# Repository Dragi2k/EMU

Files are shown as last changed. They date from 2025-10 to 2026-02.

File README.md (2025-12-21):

[][cc-by-nc-sa]

# EMU – Expandable Multi-material Unit
### A new take on a MMU by <a href="https://github.com/DW-Tas">DW-Tas</a> and <a href="https://github.com/igiannakas">igiannakas</a><br/>
<a href="https://ko-fi.com/O5O5OCC0K"> Ko-Fi</a>

**Introducing the EMU, the Expandable Multi-material Unit from down under.** The EMU is a modular, flexible, upgradable, reliable and service-friendly MMU designed around the proven filamentalist V3 platform.

The EMU supports any number of lanes and base configurations; whether it is a **single lane setup** to assist filament loading, a **dual lane configuration** for endless spool, or a **multi-lane, multi base unit setup** for multi-material printing. It is also **expandable**, with no re-printing of parts required when upgrading from a 2 lane to a multiple lane setup.

<p align="center">
  
</p>

### Table of Contents
- [Design Objectives & Key Features](#design-objectives)
- [Render Gallery](#render-gallery)
- [Prints Gallery](#prints-gallery)
- [Documentation](/docs)
  - [BOM, Printing, Assembly and Wiring instructions](/docs/assembly_wiring)
  - [Software Setup and Calibration](/docs/software_setup)
  - [Slicer setup and optimisation for multi color prints](/docs/software_setup/05-slicer-setup.md)
- [License](#this-work-is-licensed-under-a)

### Highlights
- **Modular & Expandable** design, able to add lanes anytime and in any configuration. No reprints when upgrading from a 2 lane setup.
- **One screw or tool-free** access and servicing, even mid-print.
- **Sealed dry boxes** able to maintain humidity in the 15% range (with silica gel) or 5–8% range (with molecular sieves) for weeks.  
- **Humidity sensors** per lane for filament environmental monitoring.
- **Reliable endless spool** with no chance of the rewound filament interfering with neighbouring rolls.
- **Off-the-shelf electronics** (EBB42 with EBB36 also fully compatible).  
- **Per-lane controls** - eject button + LEDs.

<p align="center">
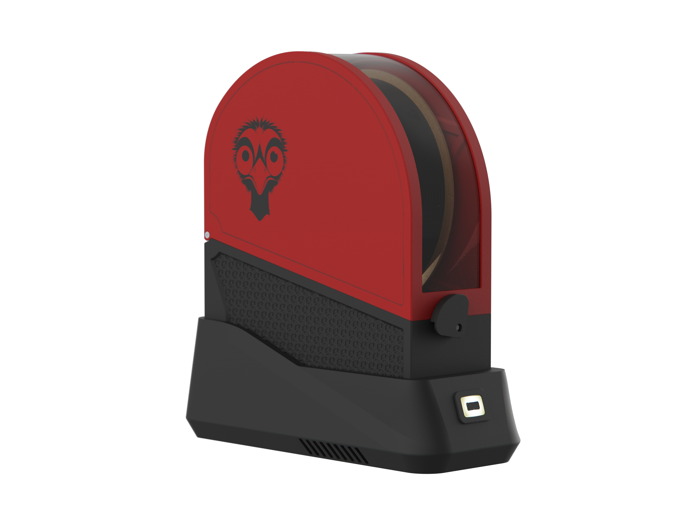
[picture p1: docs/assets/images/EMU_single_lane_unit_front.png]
  
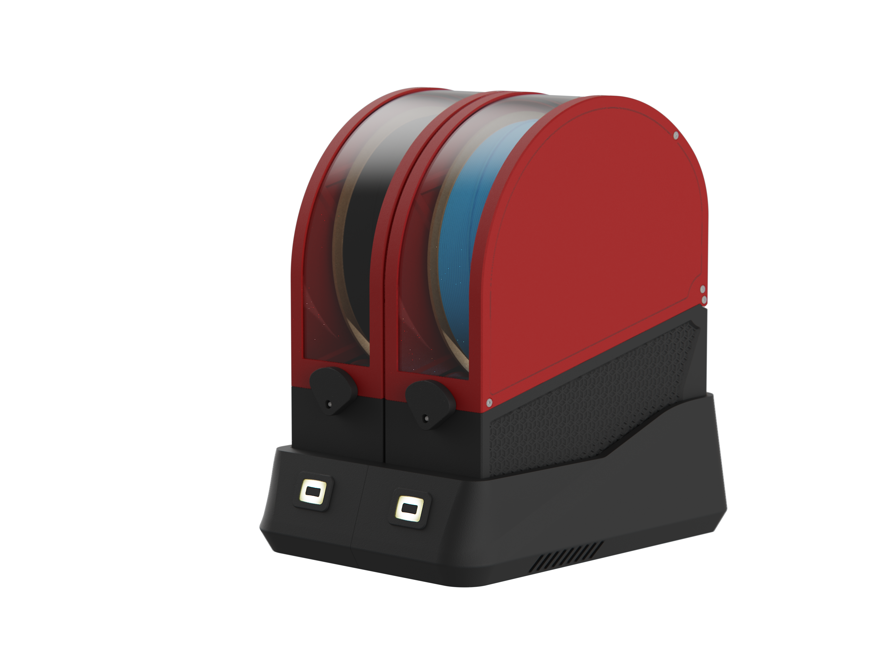
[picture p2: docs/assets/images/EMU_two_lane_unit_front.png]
  
</p>

## Design Objectives

### Modularity & Upgradeability  
Each lane is fully self-contained, so you can choose **exactly how many lanes you need and group them as you like**. You can also **mix and match** lanes across multiple base units, or use a stand-alone single lane for extruder loading and print assistance. 

Expanding later is also straightforward. Just print lane expanders for the base and add another dry box assembly. There is no need to reprint or replace existing parts when upgrading from a 2 lane base. 

### Ease of Servicing 
All electrical and mechanical components are either **one screw or completely tool-free and immediately accessible**, making live troubleshooting possible even during a print. 

Access to the electronics is easy - just lift the dry box off its base for full access. The stepper tensioning screw is accessible without any dissassembly allowing on the fly tuning of filament grip. Finally, removing the filamentalist, stepper and stepper assembly is possible via one screw.

### Sealed Dry Boxes  
Each spool sits in its own purpose built, **fully sealed dry box with an integrated desiccant holder**. The boxes use foam cord in areas of potential air ingress to create a tight seal, with the clear 1.5mm PETG/PC panel also offering visibility inside the dry box.

The dry boxes can maintain humidity in the 15% range (with silica gel) or 5–8% range (with molecular sieves) for weeks. Finally, as each dry box is self contained, opening one to reload filament, doesn’t disturb its neighbours, extending the effective desiccant life.

<p align="center">
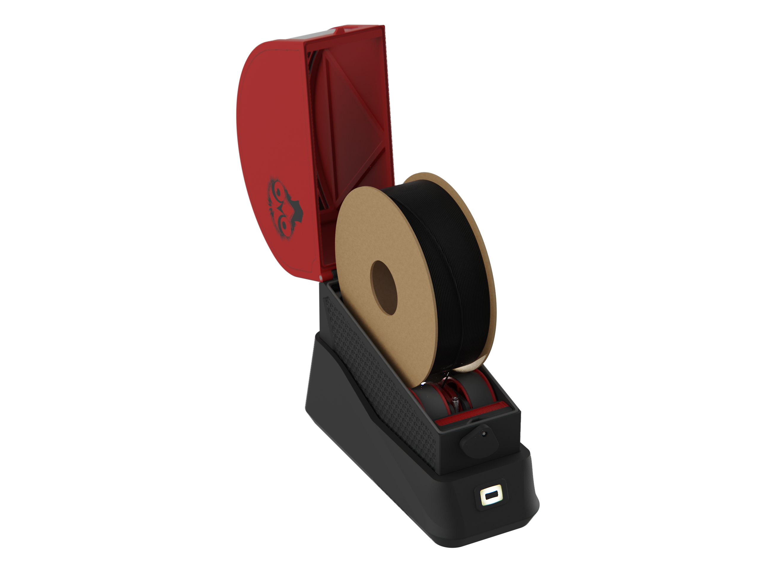
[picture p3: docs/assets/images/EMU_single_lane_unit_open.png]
  
</p>

### Integrated Humidity Sensors 
Each lane monitors its own environment, letting you know when it’s **time to refresh the desiccant**. The humidity sensors are integrated into Mainsail (and optionally in Home Assistant for historical data tracking via the mainsail HA integration).

### Endless Spool Reliability
Dual pre-stepper sensors ensure **consistent run-out detection** and reliable re-wind, as the filament is always gripped by the stepper hobbed gear assembly. 

In addition, the isolated boxes ensure that any left over, rewound, filament cannot interfere with neighbouring lanes, **preventing a jam**.

### Built on the Filamentalist
The lane assembly is based on the proven **[filamentalist V3 design with 688 bearings](https://github.com/Enraged-Rabbit-Community/ERCF_v2/tree/master/Recommended_Options/Filamentalist_Rewinder/Filamentalist_FV3_Rewinder)**, with no modifications necessary. 
- Existing 688 bearing version filamentalist parts can be reused when building an EMU.
- Optionally, the revised tensioner mount further improves pre-stepper switch actuation.
- Wide spool size compatibility - built on the 74mm filamentalist stock setup and fits even KVP filament spools.

<p align="center">
  
  
</p>

### Integrated Filament Driving Stepper 
Each lane has its own driving stepper inside the dry box, resulting in a compact, **fully self-contained mechanical design**. In case of mechanical issue, you can swap out filamentalist assemblies with 3 screws, unplugging 2 JST plugs and unplugging the bowden tube. 

In addition, you can **swap out complete dry boxes** by unplugging two JST plugs and the bowden tube. This is helpful if you want to maintain a particularly moisture sensitive filament undisturbed when swapping it out from the EMU.

### Simple Electronics
The recommended BOM uses **readily available EBB42 boards** (with EBB36 fully compatible). MMB v2 boards can also be reused, though without humidity sensing due to I²C limitations and a slightly more intricate wiring.

In addition, **each lane has its own ventilation fan**, ensuring the stepper drivers do not overheat, even when the unit is placed on top of a hot printer. With the EBB42 and EBB36, the ventilation fans can also be speed controlled to minimize noise.

### Easy mounting
The EMU base assembly can be securely **mounted on extrusions** or using **rubber feet** directly on the printer or besides it. In either case the **electronics remain accessible** without needing to remove the unit from its mounts.

### Per-lane Controls  
Each lane includes its own eject button, status LED, and a filament colour LED that illuminates the dry box. 

## Render Gallery
<p align="center">
  
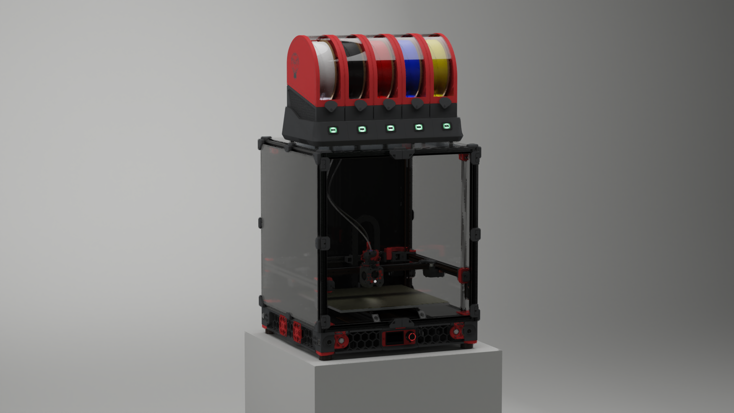
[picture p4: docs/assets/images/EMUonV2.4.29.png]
  
</p>
<p align="center">
  
  
</p>
<br/>

## Prints Gallery
<p align="center">
  1 (4)
  1 (5)
  1 (2)
  1 (3)
</p>

## This work is licensed under a
[Creative Commons Attribution-NonCommercial-ShareAlike 4.0 International License][cc-by-nc-sa].

[][cc-by-nc-sa]

[cc-by-nc-sa]: http://creativecommons.org/licenses/by-nc-sa/4.0/
[cc-by-nc-sa-image]: https://licensebuttons.net/l/by-nc-sa/4.0/88x31.png
[cc-by-nc-sa-shield]: https://img.shields.io/badge/License-CC%20BY--NC--SA%204.0-lightgrey.svg

## License clarification regarding non-commercial use:
The non-commercial aspect of this license is for cases where EMU is the product, not the use of EMU to create products.<br/>
I.e. If you wish to sell EMU as a product, you would need to seek a commercial license before doing so. </br>
It is NOT intended to prevent the use of EMU with a printer that you use to provide commercial services. If you want to run EMU in your print farm, go right ahead.

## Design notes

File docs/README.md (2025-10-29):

[][cc-by-nc-sa]

# EMU – Expandable Multi-material Unit Documentation
### A new take on a MMU by <a href="https://github.com/DW-Tas">DW-Tas</a> and <a href="https://github.com/igiannakas">igiannakas</a><br/>
<a href="https://ko-fi.com/O5O5OCC0K"> Ko-Fi</a>

<p align="center">
  
</p>

## Step 1: [Printing, assembly and wiring](/docs/assembly_wiring)
This page explains the EMU assembly and wiring. It links the BOM, detailed print settings for all of the EMU parts, including tips on how to achieve the optimal print reseults. It also includes the assembly videos, covers multi-lane and single-lane wiring for both EBB42/36 boards.

- [BOM](/docs/assembly_wiring/#bom)
- [Print Settings](/docs/assembly_wiring/#print-settings)
  - [Filamentalist components and Lane stepper components](/docs/assembly_wiring/#filamentalist-components-and-lane-stepper-components)
  - [Dry Box components](/docs/assembly_wiring/#dry-box-components)
  - [Base unit components](/docs/assembly_wiring/#base-unit-components)
- [Assembly Videos](/docs/assembly_wiring/#assembly-videos)
  - [Part 1: Filamentalist and Stepper Assembly Guide](/docs/assembly_wiring/#part-1-filamentalist-and-stepper-assembly-guide)
  - [Part 2: Drybox Assembly Guide](/docs/assembly_wiring/#part-2-drybox-assembly-guide)
  - [Part 3: Base Assembly Guide](/docs/assembly_wiring/#part-3-base-assembly-guide)
  - [Part 4: Electronics Assembly Guide](/docs/assembly_wiring/#part-3-base-assembly-guide)
- [Wiring Instructions and Diagrams](/docs/assembly_wiring/#wiring-instructions-and-diagrams)

## Step 2: [EMU board setup](/docs/software_setup/01-board-setup.md)
This page explains in detail how to setup your EMU boards with CANBus, how to flash Katapult and klipper as well as the procedure to update the klipper firmware.

- [Setting up CAN Bus](/docs/software_setup/01-board-setup.md#setting-up-can-bus)
- [Flashing the EBB boards](/docs/software_setup/01-board-setup.md#flashing-the-ebb-boards)
- [Updating the boards with the latest klipper version](/docs/software_setup/01-board-setup.md#updating-the-boards-with-the-latest-klipper-version)

## Step 3: [Happy Hare setup](/docs/software_setup/02-happy-hare-setup.md)
This page explains the step by step process to install and set up Happy Hare, the MMU management software that drives the EMU.

- [Installing Happy Hare](/docs/software_setup/02-happy-hare-setup.md#installing-happy-hare)
- [Configuring the EMU hardware](/docs/software_setup/02-happy-hare-setup.md#configuring-the-emu-hardware)
- [Configuring Happy Hare parameters](/docs/software_setup/02-happy-hare-setup.md#configuring-happy-hare-parameters)
      
## Step 4: [Calibration and startup](/docs/software_setup/03-calibration-and-startup.md)
This page explains the step by step process to calibrate the unit and the initial start up checks required to ensure successful first operation.

- [Lane rotation distance calibration](/docs/software_setup/03-calibration-and-startup.md#lane-rotation-distance-calibration)
- [Bowden tube calibration](/docs/software_setup/03-calibration-and-startup.md#bowden-tube-calibration)
- [First start up](/docs/software_setup/03-calibration-and-startup.md#first-start-up)

## Step 5: [Slicer setup and optimisation for multi color prints](/docs/software_setup/05-slicer-setup.md)
Describes the mangatory Orca slicer setup required for single extruder multi-material printing, including print profile settings to achieve optimal quality results.

- [Orca slicer mandatory setup](/docs/software_setup/05-slicer-setup.md#orca-slicer-mandatory-setup)
- [Orca slicer profile tuning for multi-color printing](/docs/software_setup/05-slicer-setup.md#orca-slicer-profile-tuning-for-multi-color-printing)

## Next steps
Once you have completed the guide above you should have a fully functioning EMU unit! Optionally you can also set up:
1. Klipper screen integration: https://github.com/moggieuk/Happy-Hare/wiki/KlipperScreen
2. Mainsail / Fluid MMU panel: https://github.com/moggieuk/Happy-Hare/wiki/Mainsail-Fluidd-Integration
3. Spoolman: https://github.com/moggieuk/Happy-Hare/wiki/Spoolman-Support

In addition, to add further lanes, follow  the instructions here: [Expanding the unit](/docs/software_setup/04-expanding-the-unit.md)

## Seeking help

The Happy Hare discord is a great resource to help you going. Both in the general channel as well as the dedicated EMU channel. Link to the discord can be found here: https://discord.gg/aABQUjkZPk

#### This work is licensed under a
[Creative Commons Attribution-NonCommercial-ShareAlike 4.0 International License][cc-by-nc-sa].

[][cc-by-nc-sa]

[cc-by-nc-sa]: http://creativecommons.org/licenses/by-nc-sa/4.0/
[cc-by-nc-sa-image]: https://licensebuttons.net/l/by-nc-sa/4.0/88x31.png
[cc-by-nc-sa-shield]: https://img.shields.io/badge/License-CC%20BY--NC--SA%204.0-lightgrey.svg

### License clarification regarding non-commercial use:
The non-commercial aspect of this license is for cases where EMU is the product, not the use of EMU to create products.<br/>
I.e. If you wish to sell EMU as a product, you would need to seek a commercial license before doing so. </br>
It is NOT intended to prevent the use of EMU with a printer that you use to provide commercial services. If you want to run EMU in your print farm, go right ahead.

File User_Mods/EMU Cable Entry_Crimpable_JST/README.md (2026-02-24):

# EMU Cable Entry with Cimpable JST sockets

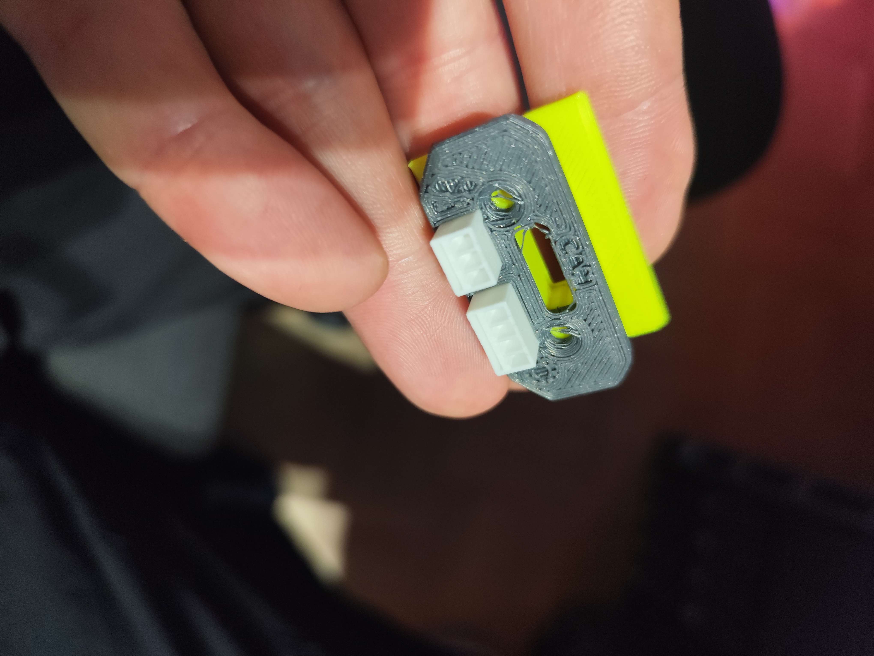
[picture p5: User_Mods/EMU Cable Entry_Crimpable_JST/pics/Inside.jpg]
Inside


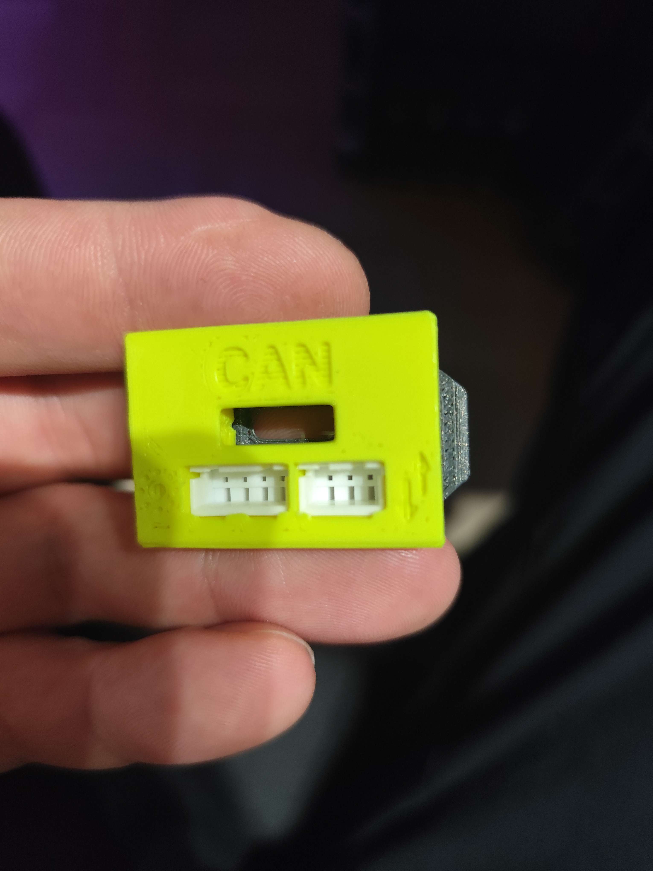
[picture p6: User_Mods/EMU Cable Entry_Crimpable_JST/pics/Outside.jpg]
Outside


for the 3 and 4 pin use these : 

https://de.aliexpress.com/item/1005008063018644.html

https://de.aliexpress.com/item/1005007287524489.html

or

https://de.aliexpress.com/item/1005009495585754.html

you need :

1x 3 pin
1x 4 pin 
per In/outled

the can bus is the origin from the BOM

by Dragi2k

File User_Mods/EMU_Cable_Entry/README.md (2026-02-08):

# EMU Cable Entry blank plate

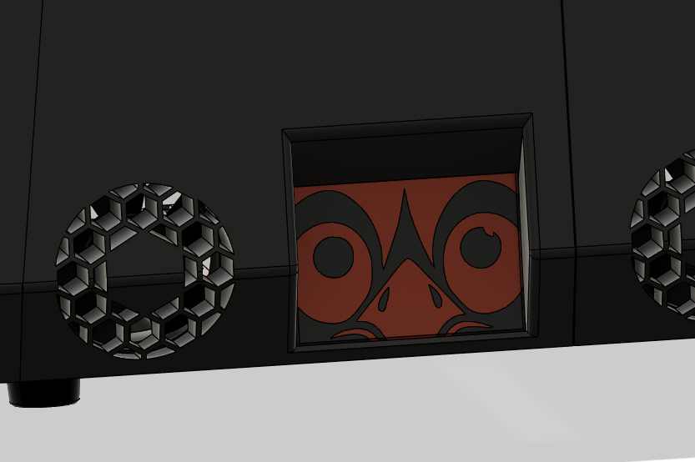
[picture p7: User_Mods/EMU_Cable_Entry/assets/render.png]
render of the plate


For those with multimaterial capabilities, or to swap in after building the EMU.  
A blank cable entry plate for the side where you don't have cables coming in. With some extra EMU flair

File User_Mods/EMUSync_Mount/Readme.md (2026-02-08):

# EMUSync_Mount

Wanted to stabalized the PSF body and not have it hanging loose in the bowden path.   Maing sure the bowden path did not have any sharp bends, curves and having the PSF as close to the EMU as possible drove the overall design.    The mounts allow for perpendicular (hanging off the back) and parallel to the extrusion mounting.

---

## Overview

It's specifically designed for the square body EMUSync in the EMU repo.   If another body type is used, a new clamp could be mounted directly to the mounting plate.   The entire clamp system can be printed without supports, and printed in the orientation with the largest flat side down.   The STL's and STEP's are filed in print orinentation.    

Assembly is straight forward simply print the parts, insert the adaptor plate in 1 of the peg holes, insert the secondary securing peg, insert the square nuts, use M3x14mm screws to secure the adaptor plate.  for best results use a M3x6 or M3x8 BHS for mounting the clamp to the adaptor plate.   M3x8mm screw to secure the clamp top

both 4040 and 2020 mounts are avialable and with the edges of the mount extended to act as panel clamp.

## Bill of Materials

### Fasteners
- 2 × M3x14 SHCS
- 2 x M3x8 SHCS
- 1 x M3 x 8 BHCS
- 3 x M3 Square Nut

### Hardware
- 1 Heat-set inserts M3×5×4)
- 3 M3 Square Nut







## Credits

This project was created by @woodworker.

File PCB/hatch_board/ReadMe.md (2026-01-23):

## EMU Wiring Hatch Board

The **EMU Wiring Hatch Board** is a dedicated PCB designed for EMU to make wiring and assembly easier and more convenient. It replaces the printed hatch ([Box_wiring_hatch](https://github.com/DW-Tas/EMU/blob/main/STL/Box/%5Ba%5D_Box_wiring_hatch.stl)), eliminates the need to solder the Filamentalist assembly wires to the JST connectors, and removes the need to use silicone to seal gaps around the JST connector.

The EMU Wiring Hatch Board was designed and developed by <a href="https://github.com/kashine6">kashine6</a>.

## Key Features

1. **Eliminates the need to solder wires directly to JST connectors**
   - Simplifies assembly
   - Reduces soldering complexity
   - Improves maintainability, as the Filamentalist assembly can be easily unplugged from inside the base unit

2. **Simplified pre-stepper sensor connections**
   - The two pre-stepper switches no longer need to be soldered in parallel. Instead, solder the sensor and ground wires to each switch individually, then plug them into the board separately.

3. **Easier box sealing**
   - Removes the need to use silicone to seal the JST connector on the hatch cover.

4. **Wire labeling**
   - Wire labels on the PCB silkscreen reduce the chance of wiring errors during assembly.

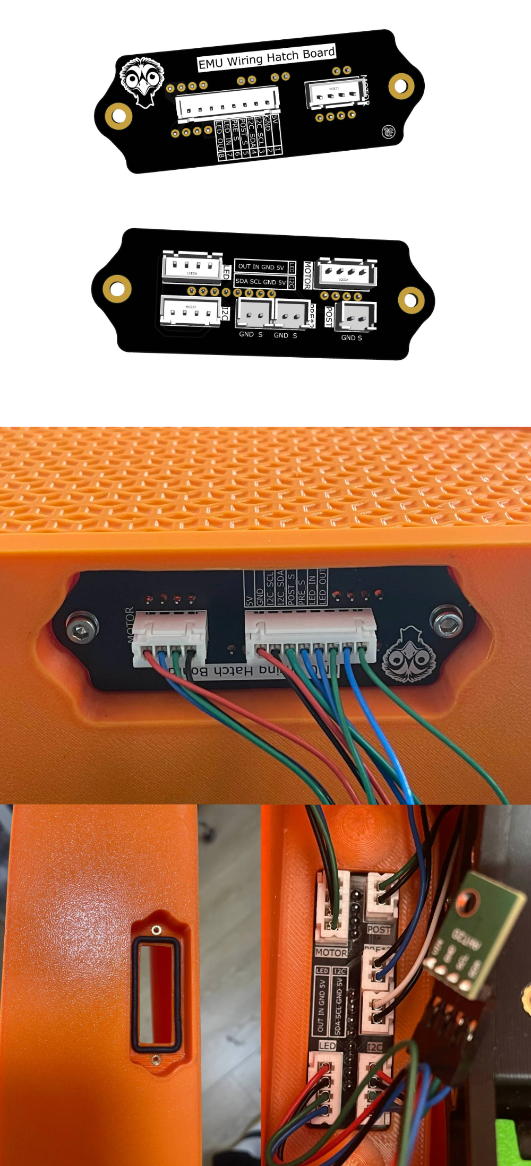
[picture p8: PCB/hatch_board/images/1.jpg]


## BOM variations vs. baseline EMU BOM
Due to the PCB being thinner than the printed box wiring hatch, **the 2x M3x8mm FHCS screws are now replaced by 2x M3x6 BHCS/SHCS screws**.

If buying pre-assembled, the corresponding straight through hole PCB header JST connectors in the BOM are no longer needed (1x JST XH 8 pin plug and 1x JST XH 4 pin plug).

If making your own and soldering the JST headers, you'll need the below JST PCB headers:
- 3x JST XH Series Straight Through Hole PCB Header, 4 Contact
- 3x JST XH Series Straight Through Hole PCB Header, 2 Contact
- 1x JST XH Series Straight Through Hole PCB Header, 8 Contact **(part of the EMU BOM)**
- 1x JST XH Series Straight Through Hole PCB Header, 4 Contact **(part of the EMU BOM)**

## Sourcing
The hatch board PCBs can be sourced from [kashine6 shop](https://www.aliexpress.com/item/1005011529532141.html) in packs of 5, or ordered DIY from JLCPCB or alternative PCB manufacturers.

## This work is licensed under a
[Creative Commons Attribution-NonCommercial-ShareAlike 4.0 International License][cc-by-nc-sa].

[][cc-by-nc-sa]

[cc-by-nc-sa]: http://creativecommons.org/licenses/by-nc-sa/4.0/
[cc-by-nc-sa-image]: https://licensebuttons.net/l/by-nc-sa/4.0/88x31.png
[cc-by-nc-sa-shield]: https://img.shields.io/badge/License-CC%20BY--NC--SA%204.0-lightgrey.svg

## License clarification regarding non-commercial use:
The non-commercial aspect of this license is for cases where EMU is the product, not the use of EMU to create products.<br/>
I.e. If you wish to sell EMU as a product, you would need to seek a commercial license before doing so. </br>
It is NOT intended to prevent the use of EMU with a printer that you use to provide commercial services. If you want to run EMU in your print farm, go right ahead.

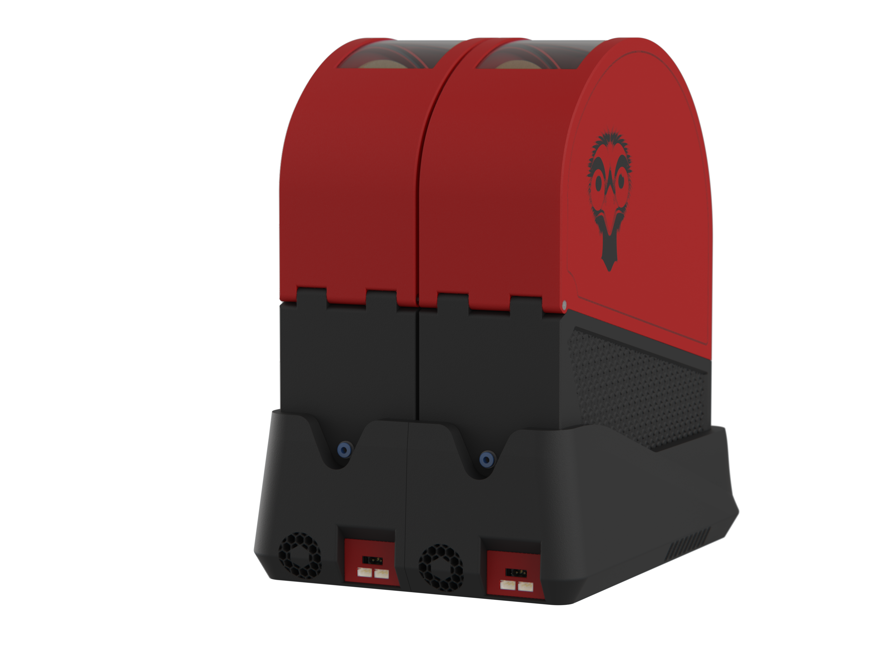
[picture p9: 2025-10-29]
docs/assets/images/EMU_two_lane_unit_rear.png

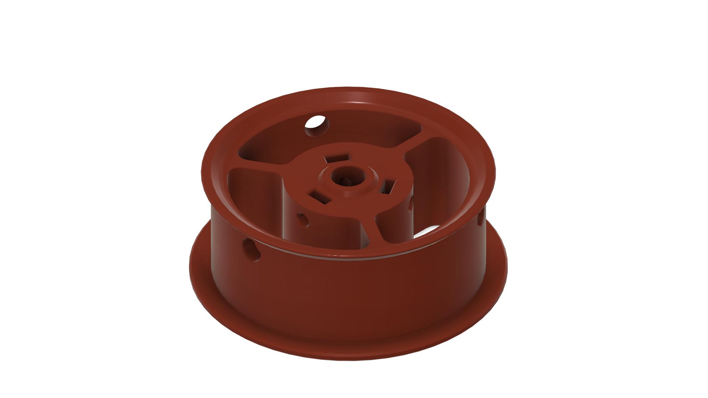
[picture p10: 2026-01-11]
User_Mods/Rim_Roller_with_square_nuts/images/Rim_roller_square_nut_3_holes.jpg

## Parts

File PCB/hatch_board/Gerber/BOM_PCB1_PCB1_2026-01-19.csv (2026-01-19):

No. | Quantity | Comment | Designator | Footprint | Value | Manufacturer Part | Manufacturer | Supplier Part | Supplier
1 | 1 | PRE*2 | CN4 | CONN-TH_2P-P2.50_HX25003-2A |  | PRE*2 | Megastar(兆星) | C7429632 | LCSC
2 | 1 | 8p | CN7 | CONN-TH_8P-P2.50-XH2.54-8P |  | 8p | Megastar(兆星) | C7429638 | LCSC
3 | 1 | SDA SCL GND 5V | I2C | CONN-TH_4P-P2.50_4PIN |  | SDA SCL GND 5V | Megastar(兆星) | C7429634 | LCSC
4 | 1 | OUT IN GND 5V | LED | CONN-TH_4P-P2.50_4PIN |  | OUT IN GND 5V | Megastar(兆星) | C7429634 | LCSC
5 | 1 | STEP | MOTOR | CONN-TH_4P-P2.50_4PIN |  | STEP | Megastar(兆星) | C7429634 | LCSC
6 | 1 | B2 B1 A1 A2 | MOTOR2 | CONN-TH_4P-P2.50_4PIN |  | B2 B1 A1 A2 | Megastar(兆星) | C7429634 | LCSC
7 | 1 | GND S | POST | CONN-TH_2P-P2.50_HX25003-2A |  | GND S | Megastar(兆星) | C7429632 | LCSC
8 | 1 | GND S GND S | PRE*2 | CONN-TH_2P-P2.50_HX25003-2A |  | GND S GND S | Megastar(兆星) | C7429632 | LCSC

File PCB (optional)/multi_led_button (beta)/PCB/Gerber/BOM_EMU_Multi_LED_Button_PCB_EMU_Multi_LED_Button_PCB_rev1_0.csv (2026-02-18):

No. | Quantity | Comment | Designator | Footprint | Value | Manufacturer Part | Manufacturer | Supplier Part | Supplier | Unique ID
1 | 4 | 100nF | C1,C2,C3,C4 | C0603 | 100nF | CL10B104KB8NNNC | SAMSUNG(三星) | C1591 | LCSC | gge7,gge8,gge9,gge10
2 | 1 | XH2.54-5P | CN1 | CONN-TH_5P-P2.54_C9900008095 |  | XH2.54-5P |  | C9900017328 | LCSC | gge2
3 | 4 | SK6812MINIRGBW-NW-P6 | LED1,LED2,LED3,LED4 | LED-ARRAY-SMD_6P-L3.7-W3.5-TL-RD-1 |  | SK6812MINIRGBW-NW-P6 | 欧思科光电 | C7423107 | LCSC | gge5,gge6,gge6_1,gge6_2
4 | 1 | TS-1088R-02026 | SW1 | SW-SMD_L3.9-W3.0-P4.45 |  | TS-1088R-02026 | XUNPU(讯普) | C455280 | LCSC | gge12

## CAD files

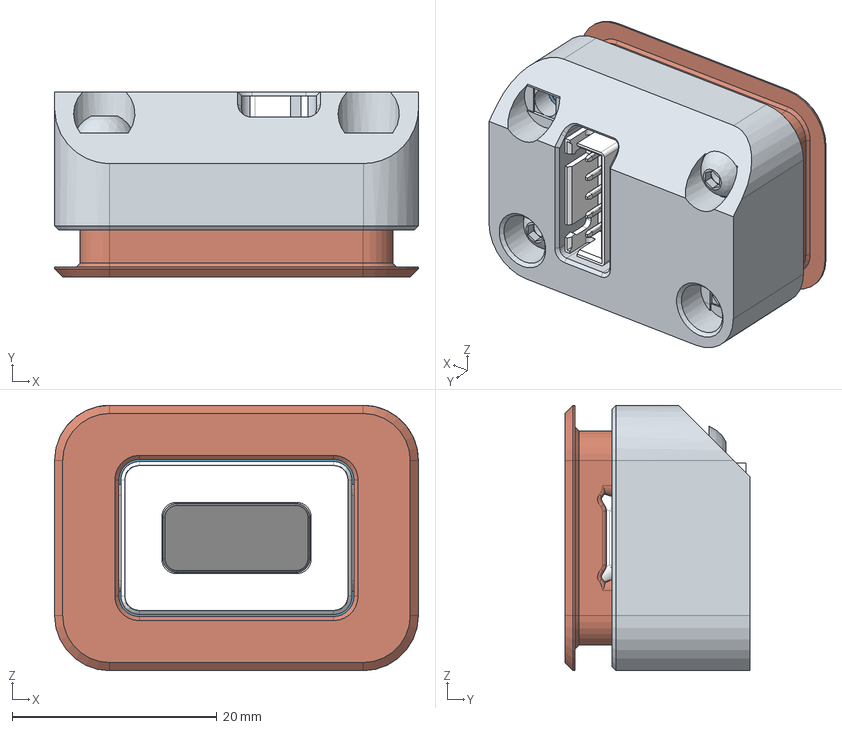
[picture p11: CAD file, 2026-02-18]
PCB (optional)/multi_led_button (beta)/CAD/Front Button Assembly - 4 LED PCB.step
35.6 x 18.1 x 26.0 mm
Button_Filter
Socket button head screw M3x0.5 x 8 x 2
[t]_Button_Diffuser
Button_Front
Button_Rear
Board~R8Az
SW-SMD_L3.9-W3.0-P4.45~SW-SMD_L3.9-W2.9-H2.0-LS4.8~R8Az
C0402~C0402_L1.0-W0.5-H0.5~R8Az x 4
LED-ARRAY-SMD_6P-L3.7-W3.5-TL-RD-1~LED-ARRAY-SMD_6P-L3.7-W3.5-TL-RD-1 ~R8Az x 4
CONN-TH_5P-P2.54_C9900008095~CONN-TH_5P-P2.54_C9900008095~R8Az

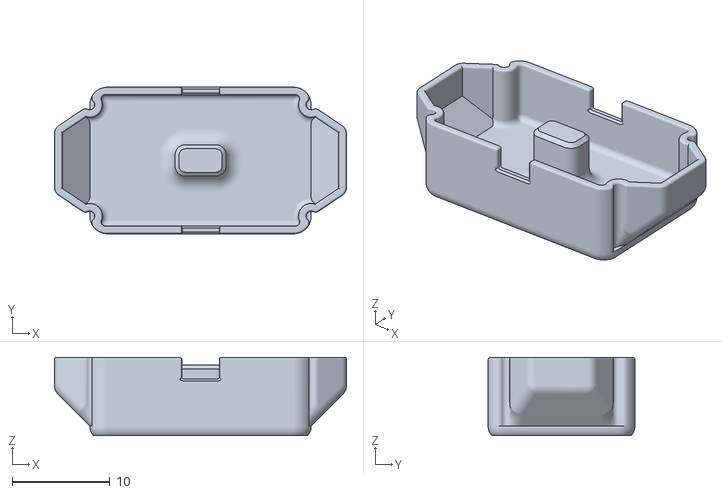
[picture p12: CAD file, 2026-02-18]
PCB (optional)/multi_led_button (beta)/STL/[t]_Button_Diffuser.stl
29.8 x 15.0 x 8.00

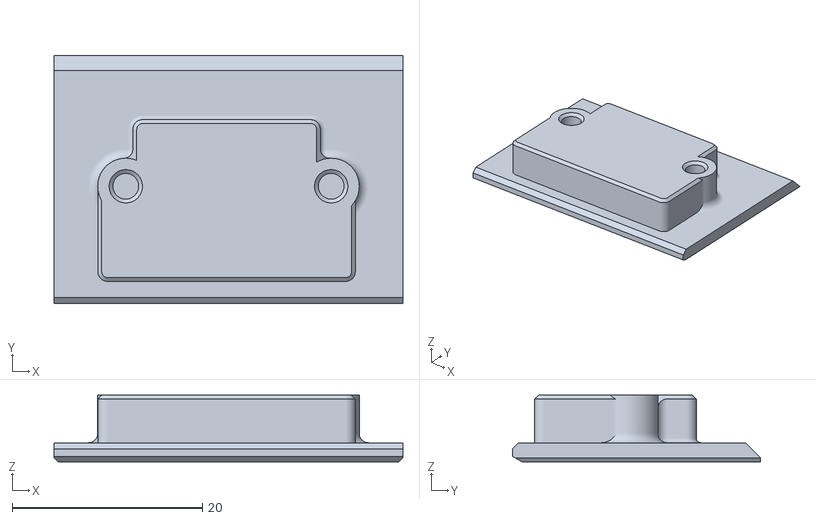
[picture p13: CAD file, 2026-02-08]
STL/Base/[a]_Cable_Entry-Outside_[blank].stl
36.7 x 26.1 x 7.00

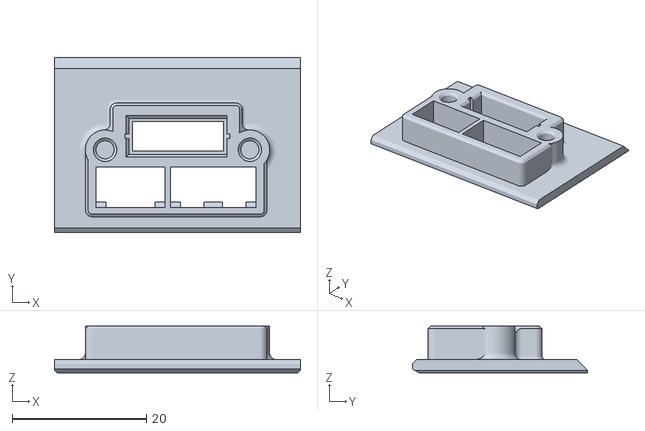
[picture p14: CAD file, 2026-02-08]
STL/Base/Optional/[a]_Cable_Entry-Outside_[CAN+sync+encoder].stl
36.7 x 26.1 x 7.00

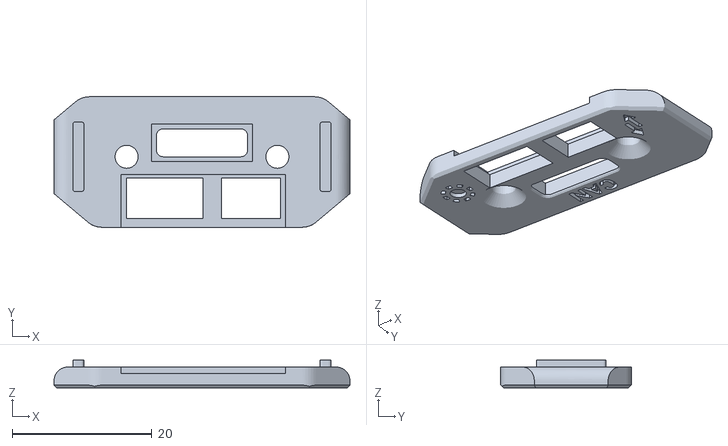
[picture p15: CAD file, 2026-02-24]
User_Mods/EMU Cable Entry_Crimpable_JST/STL/[a]_Cable_Entry-Inside_crimpable_JST.stl
42.4 x 18.7 x 4.00

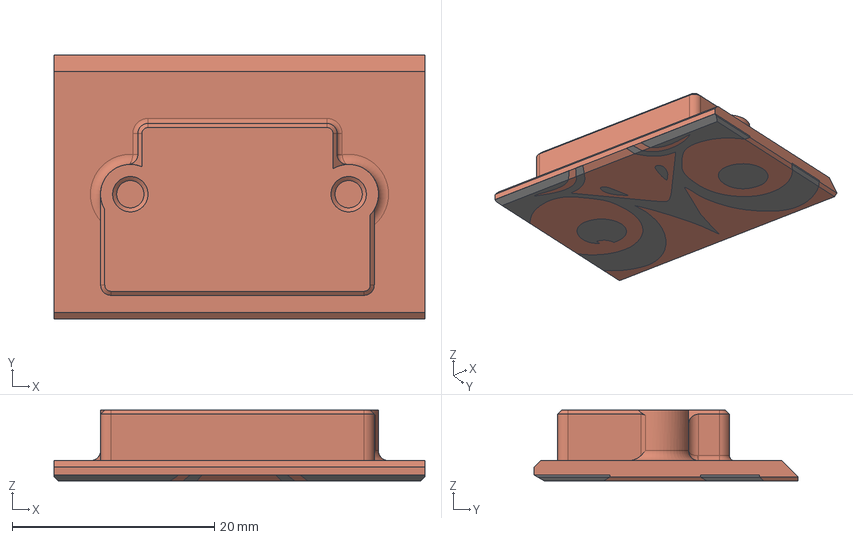
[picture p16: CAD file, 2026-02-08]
User_Mods/EMU_Cable_Entry/STEP/Cable_Entry-Outside_EMU.step
36.7 x 26.1 x 7.00 mm

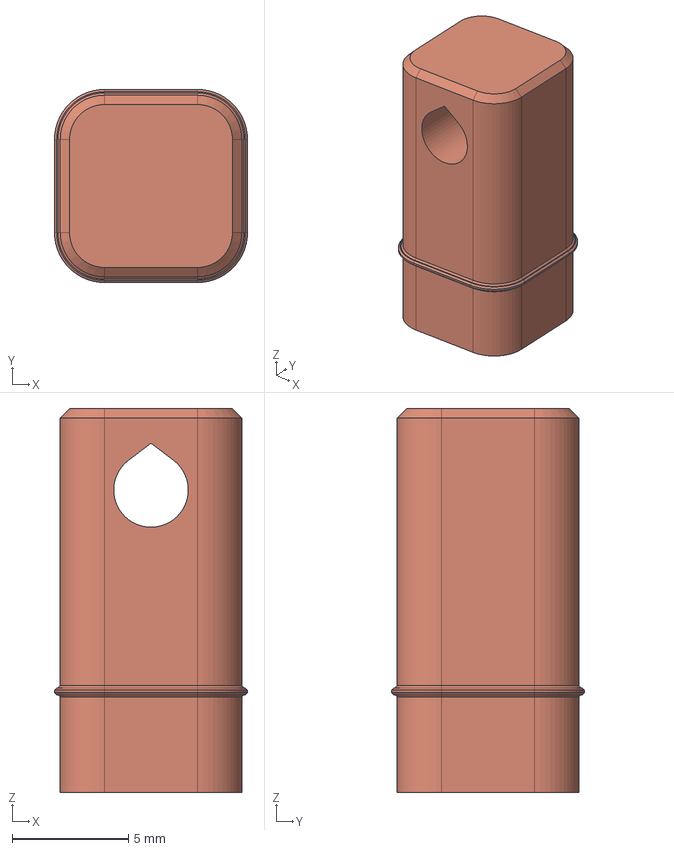
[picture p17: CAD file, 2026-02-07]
User_Mods/EMUSync_Mount/Step/PSF_Mount_Front_Resting_Pin.step
8.30 x 8.30 x 16.5 mm

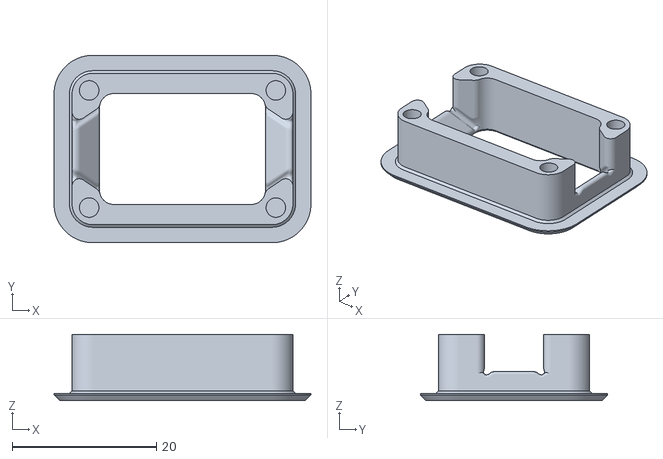
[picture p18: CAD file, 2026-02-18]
PCB (optional)/multi_led_button (beta)/STL/Button_Front.stl
35.6 x 26.0 x 9.20

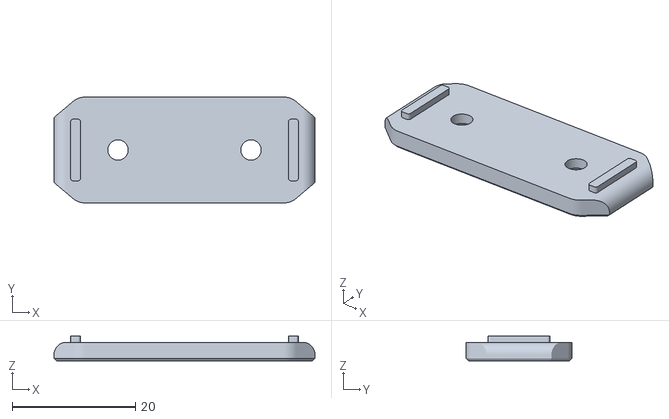
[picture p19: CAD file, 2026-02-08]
STL/Base/[a]_Cable_Entry-Inside_[blank].stl
42.4 x 17.2 x 4.00

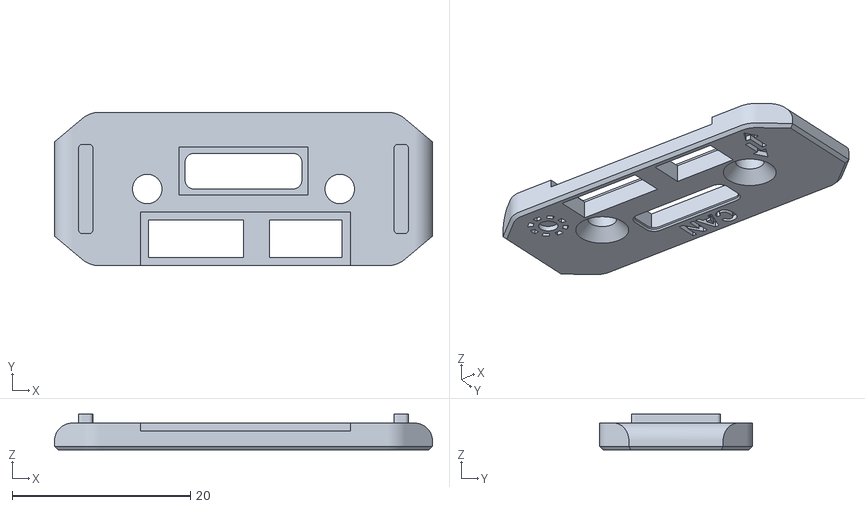
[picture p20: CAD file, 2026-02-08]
STL/Base/Optional/[a]_Cable_Entry-Inside_[CAN+sync+encoder].stl
42.4 x 17.2 x 4.00

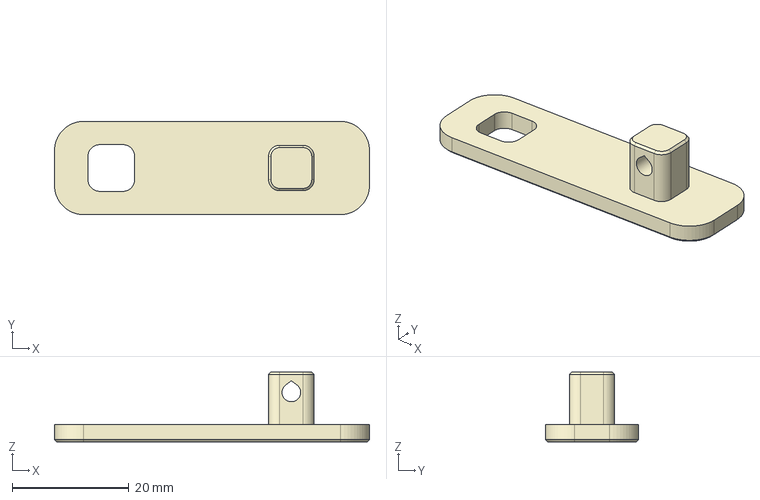
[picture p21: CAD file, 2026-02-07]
User_Mods/EMUSync_Mount/Step/PSF_Mount_Adaptor_Plate.step
54.0 x 16.0 x 12.0 mm

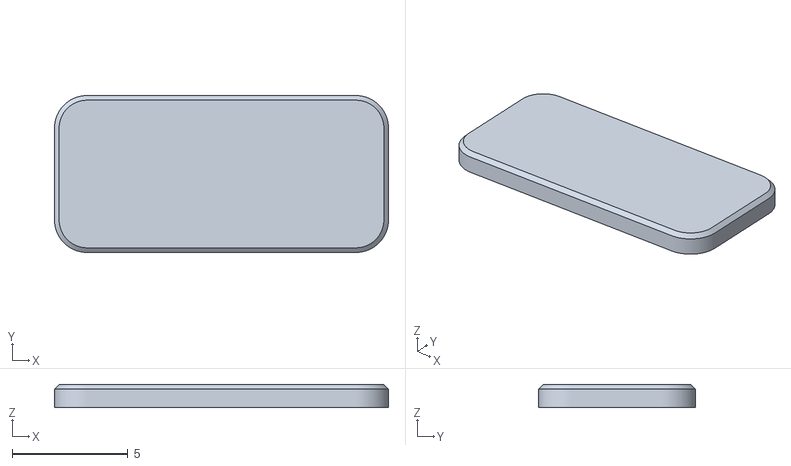
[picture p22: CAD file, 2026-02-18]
PCB (optional)/multi_led_button (beta)/STL/Button_Filter.stl
14.4 x 6.76 x 1.00

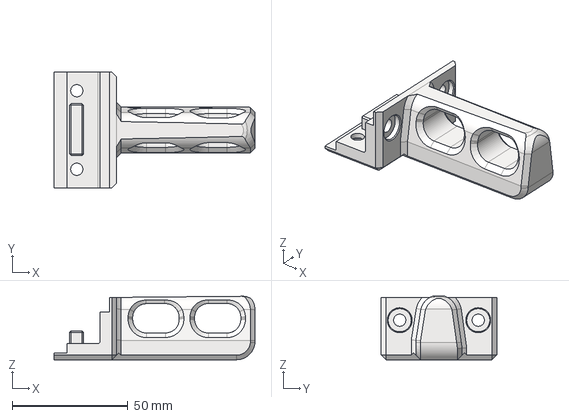
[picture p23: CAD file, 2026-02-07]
User_Mods/EMUSync_Mount/Step/PSF_2020_Mount_Perpendicular.step
87.0 x 50.0 x 27.5 mm

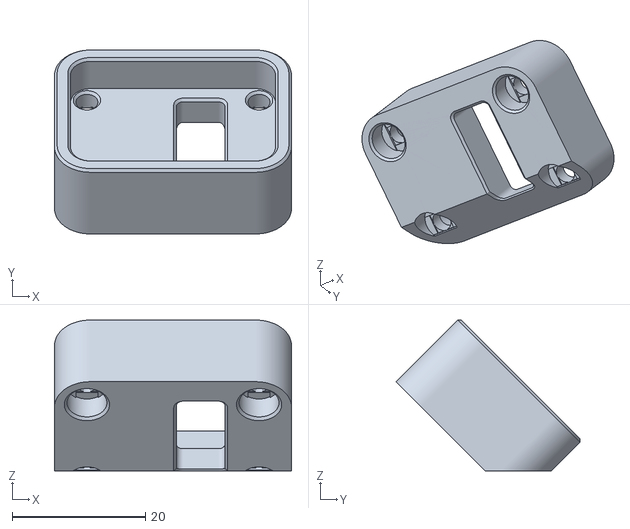
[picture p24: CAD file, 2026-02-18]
PCB (optional)/multi_led_button (beta)/STL/Button_Rear.stl
35.6 x 27.6 x 22.7

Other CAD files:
User_Mods/EMU Cable Entry_Crimpable_JST/STL/[a]_Cable_Entry-Outside_crimpable_JST.stl
STL/Base/[a]_Cable_Entry-Inside.stl
STL/Base/[a]_Cable_Entry-Outside.stl
User_Mods/EMUSync_Mount/Step/PSF_4040_Mount_Perpendicular.step
User_Mods/EMUSync_Mount/STL/PSF_2020_Mount_Parallel.stl
User_Mods/EMUSync_Mount/STL/PSF_2020_Mount_Perpendicular.stl
User_Mods/EMUSync_Mount/STL/PSF_4040_Mount_Parallel.stl
User_Mods/EMUSync_Mount/STL/PSF_4040_Mount_Perpendicular.stl
User_Mods/EMUSync_Mount/STL/PSF_Mount_Adaptor_Plate.stl
User_Mods/EMUSync_Mount/STL/PSF_Mount_EMUSynch_Clamp.stl
User_Mods/EMUSync_Mount/STL/PSF_Mount_Front_Resting_Pin.stl
User_Mods/EMUSync_Mount/Step/PSF_2020_Mount_Parallel.step
User_Mods/EMUSync_Mount/Step/PSF_4040_Mount_Parallel.step
User_Mods/EMUSync_Mount/Step/PSF_Mount_EMUSynch_Clamp.step
User_Mods/EMU_Cable_Entry/3MF/Cable_Entry-Outside_EMU.3mf
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

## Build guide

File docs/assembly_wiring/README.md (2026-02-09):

# EMU - BOM, Printing, Assembly and Wiring Guide

## Table of Contents
- [EMU - BOM, Printing, Assembly and Wiring Guide](#emu---bom-printing-assembly-and-wiring-guide)
  - [Table of Contents](#table-of-contents)
  - [BOM](#bom)
  - [Print Settings](#print-settings)
    - [Filamentalist components and Lane stepper components:](#filamentalist-components-and-lane-stepper-components)
    - [Dry Box components:](#dry-box-components)
    - [Base unit components:](#base-unit-components)
  - [Assembly Videos](#assembly-videos)
    - [Part 1: Filamentalist and Stepper Assembly Guide](#part-1-filamentalist-and-stepper-assembly-guide)
    - [Part 2: Drybox Assembly Guide](#part-2-drybox-assembly-guide)
    - [Part 3: Base Assembly Guide](#part-3-base-assembly-guide)
    - [Part 4: Electronics Assembly Guide](#part-4-electronics-assembly-guide)
    - [Part 5: EMU Sync Assembly images](#part-5-emu-sync-assembly-images)
    - [Combiner:](#combiner)
  - [Wiring Instructions and Diagrams](#wiring-instructions-and-diagrams)
  - [Wiring key dimensions](#wiring-key-dimensions)
    - [Base wiring dimensions](#base-wiring-dimensions)
    - [PCB Hatch wiring dimensions](#pcb-hatch-wiring-dimensions)
    - [DIY Hatch (no pcb) wiring dimensions](#diy-hatch-no-pcb-wiring-dimensions)

<p align="center">
  
</p>

## BOM  
The EMU Bill of Materials can be found here: [Draft BOM](https://docs.google.com/spreadsheets/d/1jYJXBgpc_iLDfC17fC2LTYKrSEy5ocPbGEQ_EEOGCvI)

**Recommended optional extras:**
1. [PCB hatch boards](https://github.com/DW-Tas/EMU/tree/main/PCB%20(optional)/hatch_board) - simplifies wiring.
2. [Proportional Sync Feedback Sensor](https://www.aliexpress.com/item/1005010470743517.html) - allows for clog, tangle detection and more accurate syncronisation between the EMU and the extruder.

## Print Settings

### Filamentalist components and Lane stepper components:
The below print settings are recommended for the filamentalist and lane stepper components. These are structural parts hence require print settings optimised for strength:
- 0.2 mm layer height
- 0.2 mm first layer height
- 4 walls
- 40% infill
- 0.4mm extrusion width (line width) throughout
- Gyroid sparse infill is recommended as it tends to warp less
- Inner Outer wall ordering, to ensure overhangs and supported areas do not sag
- Arachne wall generator
- One wall top and bottom surfaces (optional but recommended - parts look nicer)
- Disable thick bridges
- Z hop enabled to avoid nozzle scraping (0.2 is sufficient)

> [!IMPORTANT]
> **Parts are not shrinkage compensated** - calibrate your filament shrinkage first! If the bearings are loose, you're either under extruding, or over compensating for shrinkage.<br/>
> **Disable thick bridges** in your slicer and make sure your flow rate (EM) is on point! **Over extrusion, thick bridges and insufficient cooling will cause your sensor magnets and bearings not to fit as the bridges will sag.**

**For the TPU filamentalist CDR ring:**
- 0.2 mm layer height
- 0.2 mm first layer height
- 0.4mm extrusion width (line width) throughout
- 6 walls, so that the object is printed solid
- Avoid crossing walls enabled
- Random seam. This is important to avoid an aligned seam bump
- Inner Outer wall ordering, to ensure overhangs and supported areas do not sag
- Z Hop turned off to reduce stringing
  
> [!IMPORTANT]
> Printing TPU can be a challenge - print by object and a slight negative (-0.1) extra length on retract can help reduce stringing.

### Dry Box components:
The below print settings are recommended for the dry boxes and the desiccant holder. The dry boxes need to be as air tight as possible, hence the recommended print settings below are tuned to achieve this while keeping filament use under control.
- 0.2 mm layer height
- 0.2 mm first layer height
- 3 walls
- 15% infill
- For the lid specifically, use 4 walls and 30% infill to ensure strength in the front lip.
- 0.4mm extrusion width (line width) throughout
- Gyroid sparse infill is recommended as it tends to warp less
- Inner Outer wall ordering, to ensure dry box hatch features print with minimal sagging.
- Arachne wall generator
- One wall top and bottom surfaces (optional but recommended - parts look nicer)
- Disable thick bridges
- Z hop enabled to avoid nozzle scraping (0.2 is sufficient)

> [!IMPORTANT]
> Print with **extra first layer squish, use an adhesion promoter on the bed and in a pre-heated chamber with low fan** to prevent warping and ensure better layer adhesion. Mouse ears on the box corners may be required. Slight lifting will not impact part function.<br/>
> **Do not use mouse ears on the lid** as the slicer wrongly fills in the aesthetic lines.<br/>
> **Over extrude (only) the box and lid by ~2% (0.02)** to ensure air tightness. Increase your slicer flow multiplier (EM) by 0.02.

### Base unit components:
The below print settings are recommended for the base units and their accessories. 
- 0.2 mm layer height
- 0.2 mm first layer height
- 3 walls
- 15% infill
- 0.4mm extrusion width (line width) throughout
- Gyroid sparse infill is recommended as it tends to warp less
- Inner Outer Inner wall ordering to improve visual appearance
- Arachne wall generator
- One wall top and bottom surfaces (optional but recommended - parts look nicer)
- Disable thick bridges
- Z hop enabled to avoid nozzle scraping (0.2 is sufficient)
- For the **Eject button lens, 99 walls are recommended,** to reduce possibility of infill shining through the natural ABS

> [!IMPORTANT]
> Print with **extra first layer squish, use an adhesion promoter on the bed and in a pre-heated chamber with low fan** to prevent warping. Slight lifting will not impact part function.

> [!NOTE]
> **Paint on fuzzy skin** on the outer walls of the base unit will improve appearance.<br/>
> Paint on ONLY, not full model fuzzy skin. <br/>
> 0.1 distance, 0.1 or 0.2mm depth. Displacement method (orca slicer)

## Assembly Videos

### Part 1: Filamentalist and Stepper Assembly Guide
EMU Filamentalist and Stepper Assembly Guide (https://www.youtube.com/watch?v=FNcXC9HXUmI)
<br/>
**Errata:**
1. BMG Gear insertion is not visible in the video. Do this before adding the stepper main body and screwing it on.
2. Switch sensor screws are M2x10 self taping or m2x8 bhcs/shcs
3. Filament path - BMG gear alignment step is not shown in the video. Insert some filament through the unit manually, loosen the BMG gear set screw and move it back and forth. Screw down the BMG gear.
4. For the BMG tensioning arm, the bushing is no longer an option. 
5. Add a washer to the stepper tensioning arm on both sides of the spring.
6. Stepper body screws are all M3x20
7. Front ECAS is no longer required
8. PTFE tube lengths have been updated since the video release. [Use the dedicated cutter STL](https://github.com/DW-Tas/EMU/blob/main/STL/Tools/PTFE%20Cutter%20and%20Length%20Tool.stl) to measure and cut the PTFE tubes.

### Part 2: Drybox Assembly Guide
EMU Dry Box Assembly Guide (https://www.youtube.com/watch?v=JZzMyOBCdSM)
<br/>

**Errata:**
1. A threaded stand off is inserted in the front lip of the lid and secured from either side with M3x40 FHCS bolts.
2. Box and wiring hatch changes - the wiring hatch now is screwed in from the outside of the unit. Push through the hole from the inside out and then screw in place.
3. Wiring hatch foam is now glued on the box itself. The foam chord channel is on the outside of the box. 
4. The BME sensor has been relocated to the LED cover.

### Part 3: Base Assembly Guide
EMU Base Assembly Guide (https://www.youtube.com/watch?v=2SmAMuXas38)
<br/>

### Part 4: Electronics Assembly Guide
EMU Elecrronics Assembly Guide (https://www.youtube.com/watch?v=Iang2JYkTh8)
<br/>

**Errata:**
1. Base unit top clamping screws (M3x8 FHCS) now screw into heatset inserts inserted on the other side of the frame.
2. External combiner sensor is no longer specified in the default setup. That wiring part can be omitted.
3. Encoder is no longer specified in the default setup. That wiring part can be omitted.
4. Wiring is performed using the legacy method where a single LED chain was being created tied to the first EBB board. Current wiring approach wires each lane's LED's to the corresponding lane EBB, effectively moving away from one chain to N chains, where N is the number of lanes in the system. This simplifies wiring greatly and contains the wiring for each lane within the lane itself.
5. CANbus entry wires (Yellow/Green) are now connected directly to the first lane EBB42/36, ommiting the WAGO connectors. Only the power wires and LED signal wire are now connected to the WAGO connectors.

### Part 5: EMU Sync Assembly images
<table>
  <tr>
    <td>Step 1</td>
    <td>Step 2</td>
    <td>Step 3</td>
  </tr>
  <tr>
    <td>Step 4</td>
    <td>Step 5</td>
    <td>Step 6</td>
  </tr>
  <tr>
    <td>Step 7</td>
    <td>Step 8</td>
    <td>Step 9</td>
  </tr>
  <tr>
    <td>Step 10</td>
    <td>Step 11</td>
    <td>Step 12</td>
  </tr>
  <tr>
    <td>Step 13</td>
    <td>Step 14</td>
    <td>Step 15</td>
  </tr>
</table>

### Combiner:
Make sure the PTFE tube is pushed all the way inside the combiner. Not just at the ecas entry!



## Wiring Instructions and Diagrams
Depending on the number of lanes assembled, the wiring will vary slightly. Below are some initial wiring key notes to get your started.<br/>

**Wiring notes**
1. Please note that the sync feedback sensor is connected to the first lane board.
2. The CAN bus umbilical from the printer feeds power and the CAN H / L wires to the WAGO connectors in the first lane. 
3. A 24V and Ground "bus" is established throughout the base unit using the two rear WAGO connectors (WAGO 3 and WAGO 4).
4. The EBB boards connect to the power bus for power and plugged in using their Molex ports.
5. The EBB boards are daisy chained to establish the CANbus network. The first lane canbus High / Low are connected to the box cable entry and power from the first lane WAGOs (wago 3 and 4).
7. The second lane canbus High / Low wires are connected to the CAN out dupont connectors on the first board itself. This creates the daisy chain.
9. The last EBB board needs the 120Ohm resistor installed.
10. Each lane's 2nd WAGO connector is used to connect the Neopixel Out wire from the eject button to the Neopixel In wire on the dry box.

**Adding a second base unit** <br/>
You can daisy chain as many base units as you desire. Simply wire the XT30+2 CAN out port next to the last lane to the power bus and CAN H / L dupont connectors on the last EBB board. The next base unit can connect using a standard CAN Bus cable to the first unit.

**EBB 42 wiring diagram**<br/>
<p align="center">
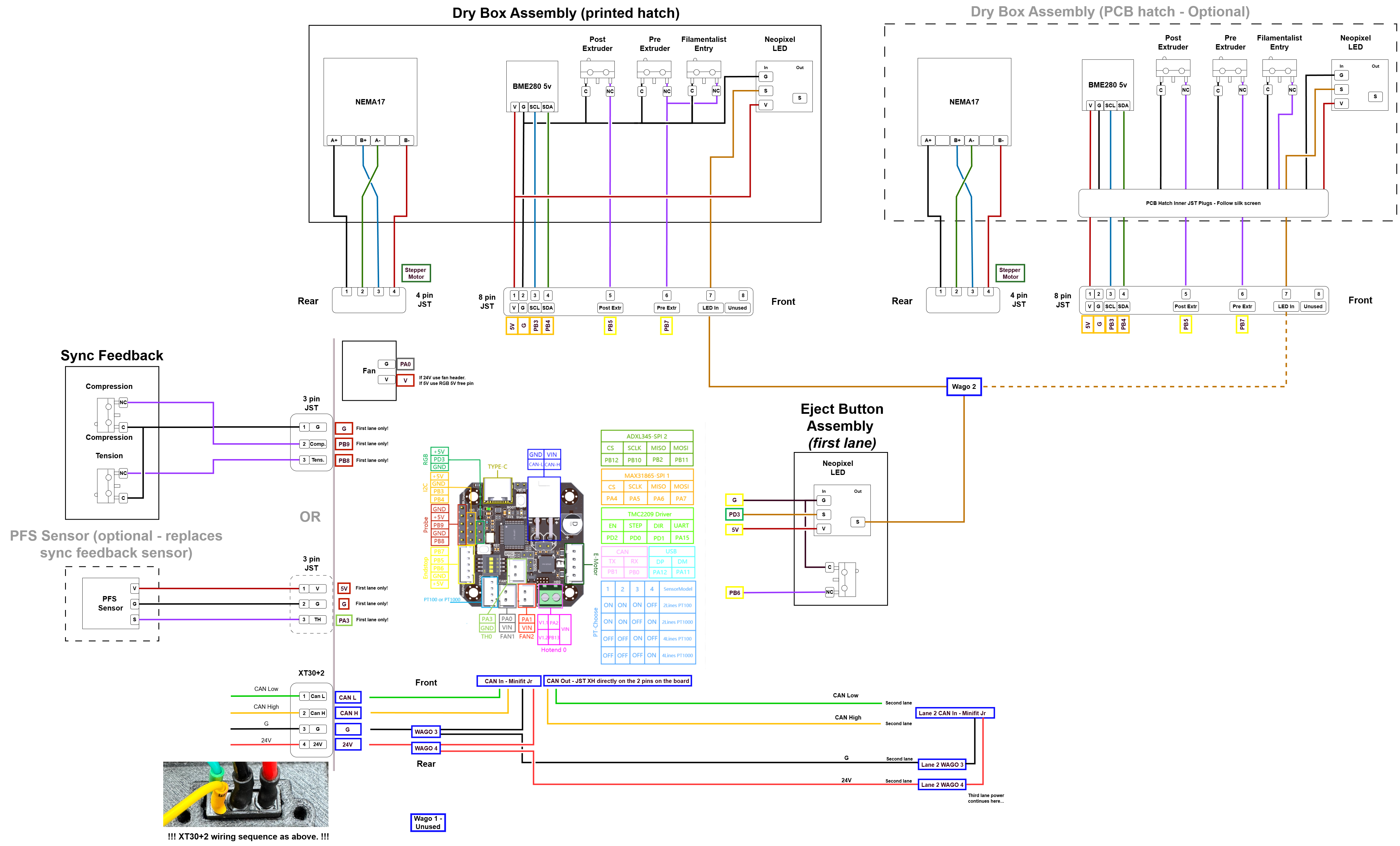
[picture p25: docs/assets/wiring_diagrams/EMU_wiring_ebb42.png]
  
</p>

**Printer PSU**<br/>
> [!WARNING]
> You need to evaluate whether your PSU has enough power headroom. This entirely depends on your printer's overall setup. Ideally **plan for ~20 Watts for an 5 lane MMU** with **each additional lane requiring approximately an additional ~2-2.5 Watts.**

Key factors to consider:
1. PSU wattage
2. How many A-B/X-Y and Z steppers 
3. At what current the main printer steppers are operating at and what print speeds you operate them at
4. Your heater cartridge wattage 
5. What other power consuming accessories are connected to the printer (cpap, heater bed if 24V etc)

Depending on the combined power consumption, you may need to consider whether a PSU upgrade is needed. 

As a rule of thumb, a 12 lane EMU build with 4 Z steppers and 2 AB steppers running moderately high currents and high print speeds on a Voron 2.4 may require a 350Watt power supply to ensure adequate power headroom.

## Wiring key dimensions

This parts describes the recommended wire length for easy assembly and maintenance.

### Base wiring dimensions

<p align="center">
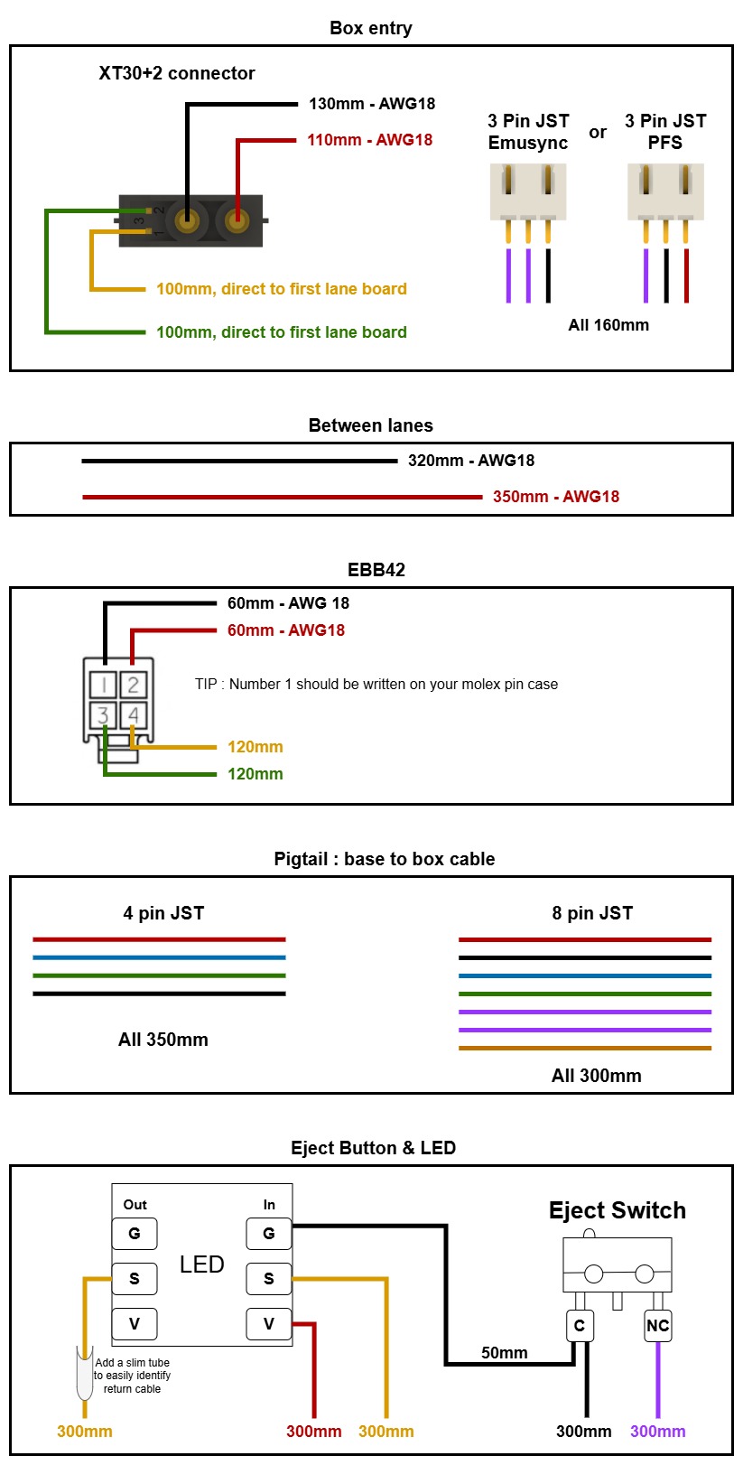
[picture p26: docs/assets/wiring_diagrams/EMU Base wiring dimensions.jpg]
  
</p>

### PCB Hatch wiring dimensions
> These dimensions are for the latest version of the PCB (Post sensor at the rear). If you have the older board (Post Sensor at the center) [refer to this image](../assets/wiring_diagrams/EMU%20PCB%20Hatch%20wiring%20dimensions%20-%20Old%20PCB.jpg) for sensor wire lengths.
<p align="center">
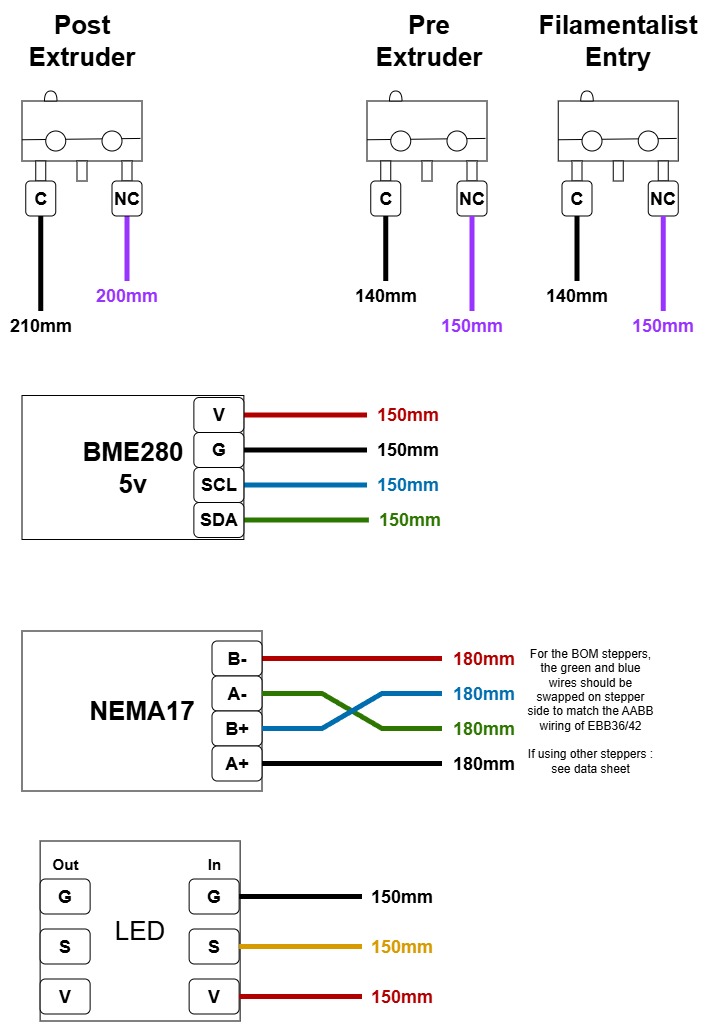
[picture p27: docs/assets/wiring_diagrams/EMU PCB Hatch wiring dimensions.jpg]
  
</p>

### DIY Hatch (no pcb) wiring dimensions

> These wiring dimensions assume you mount the BME sensor on the led cover and connect `5V` and `Ground` of the BME sensor to the led out `5V` and `Ground`.

<p align="center">
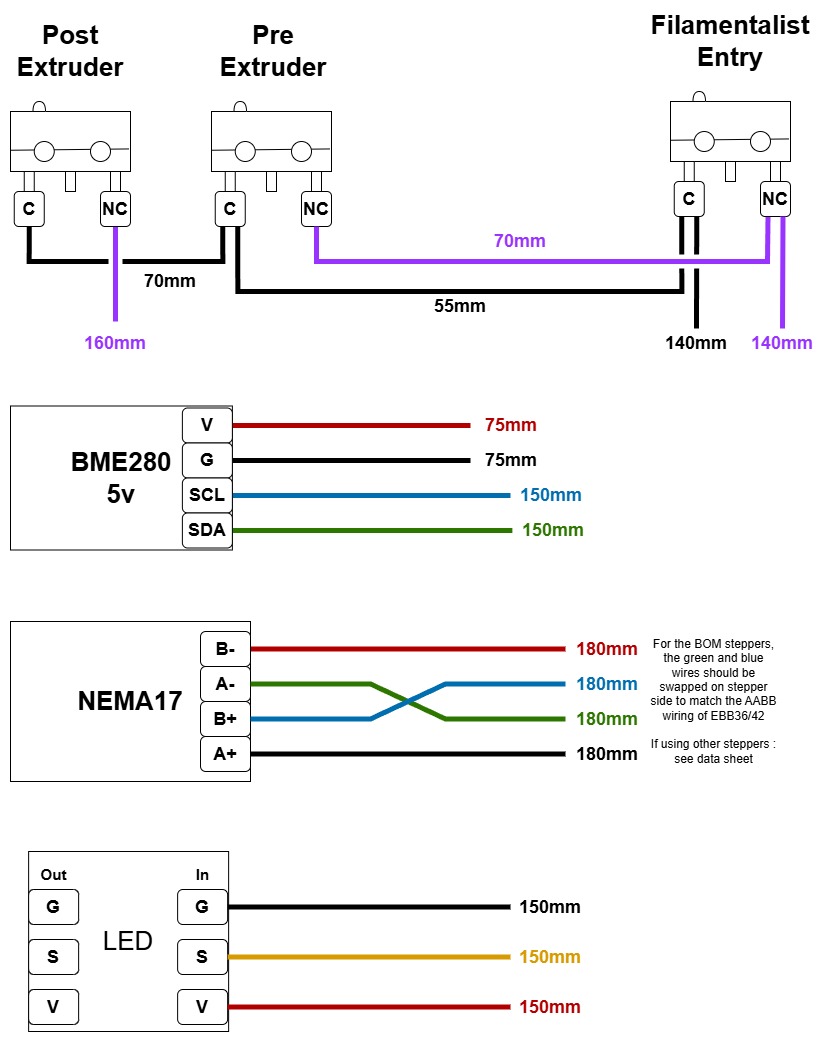
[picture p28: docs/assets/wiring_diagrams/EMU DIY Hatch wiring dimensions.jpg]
  
</p>

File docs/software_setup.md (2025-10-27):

# EMU Happy Hare Hardware and Software Setup Guide

This is a provisional sofware setup guide for the EMU using Happy Hare v3. This guide is meant to be read in conjunction with the Happy Hare setup guide as found here: https://github.com/moggieuk/Happy-Hare/wiki

## Table of Contents

- [Setting up CAN Bus](#setting-up-can-bus)
- [Flashing the EBB boards](#flashing-the-ebb-boards)
- [Updating the boards with the latest klipper version](#updating-the-boards-with-the-latest-klipper-version)
- [Setting up Happy Hare](#setting-up-happy-hare)
- [Configuring the EMU hardware in Happy Hare](#configuring-the-emu-hardware-in-happy-hare)
- [Configuring Happy Hare](#configuring-happy-hare)
- [Calibrating the unit](#calibrating-the-unit)
- [First start up](#first-start-up)
- [Next steps](#next-steps)

## Setting up CAN Bus
If your printer does not have canbus set up, follow the excellent guide from Esoterical here: https://canbus.esoterical.online. If you are not familiar with CAN Bus, read through the guide from Esoterical. **CAN Bus is simple to set up and operate, but please do read the guide to familiarise yourselves with the CAN Bus concepts and terminology.**

Do not forget to terminate the last EBB board or CANBus device in your bus (depending on your bus topology).

## Flashing the EBB boards
Prior to setting up the EMU, the EBB boards need to be flashed with Katapult and Klipper. Flashing instructions can be found here https://canbus.esoterical.online/toolhead_flashing.html. The boards are flashed in exactly the same way as if they were used as a toolhead board. Below are some high level instructions; however do refer back to the guide by Esoterical for a more comprehensive guide.<br/>

**Step 1:** Install katapult:<br/>
Katapult is a piece of software that sits on the EBB units (and any CAN Bus device) and acts as an easy way to set your board in "flashing mode" making klipper updates super easy. It is highly recommended that Katapult is flashed on the boards.
```
test -e ~/katapult && (cd ~/katapult && git pull) || (cd ~ && git clone https://github.com/Arksine/katapult) ; cd ~
```
**Step 2:** Connect your first EBB board over USB **outside the EMU**. Make sure the **power by USB jumper is set**.<br/>
**Step 3:** Set the board in DFU mode by pressing and holding the reset and boot buttons. Release the reset button first, then release the boot button<br/>
**Step 4:** The board should show as in DFU mode. Run ```lsusb``` and check that something like the below is shown in the command line:<br/>
```
Bus 001 Device 005: ID 0483:df11 STMicroelectronics STM Device in DFU Mode
```
**Step 5:** initiate menuconfig for Katapult.<br/>
```
cd ~/katapult
make menuconfig
```


```
make
```
**Step 6:** Flash katapult to the EBB board<br/>
```
sudo dfu-util -R -a 0 -s 0x08000000:mass-erase:force:leave -D ~/katapult/out/katapult.bin -d 0483:df11
```
**Step 7:** initiate menuconfig for klipper and make the firmware<br/>
```
sudo service klipper stop
cd ~/klipper
make clean
make menuconfig
```

```
make
```
**Step 8:** Prepare to flash klipper<br/>
Now that katapult is loaded, unplug the USB cable, remove the USB power jumper (if installed) and install the EBB on the unit. Power it via the canbus pigtail.

Please note, **you can set up katapult on all the boards and install them back to the unit all at once**. However, identifying which board is which from the UID is more tricky if you have them all installed in the unit. 

You have two options to identify them.
1. Unplug the positive (red) wire from the wagos for all the boards except the one you are intending to flash klipper, Run the command from Step 9, note the UUID, flash klipper and note down the UUID you just used with the lane number in your documentation  _--or--_
2. Run the command from Step 9, pick one UUID, flash Klipper, note which board's led stopped flashing and note down the UUID you just used with the lane number in your documentation.

**Step 9:** Find the board UUID<br/>
Run the command below and note the produced UUID
```
python3 ~/katapult/scripts/flashtool.py -i can0 -q
```
**Step 10:** Flash klipper<br/>
```
python3 ~/katapult/scripts/flashtool.py -i can0 -f ~/klipper/out/klipper.bin -u youruuid
```
**Flashing the remaining boards:** <br/>

Repeat step 2 (connect via USB),3 (set in DFU mode),4 (lsusb to confirm DFU),6 (flash katapult),8 (install the board),9 (pick the UUID),10 (flash klipper) for each subsequent board. Please note that as the boards are the same you do not need to re-run the menu config and make process.

> [!IMPORTANT]
> Remember to note down the UUID - Lane values for your reference. This combination will be used later in the guide to set up Happy Hare.

## Updating the boards with the latest klipper version
```
sudo service klipper stop
cd ~/klipper
make clean
make menuconfig
make
python3 ~/katapult/scripts/flashtool.py -i can1 -u youruuid -r
python3 ~/katapult/scripts/flashtool.py -i can1 -u youruuid -f ~/klipper/out/klipper.bin
```
Repeat the last two steps for each EBB board. Note the uuid used with the lane number in your documentation. This will be used later.

## Setting up Happy Hare
Install Happy Hare. More detailed instructions can be found here: https://github.com/moggieuk/Happy-Hare/wiki/Installation
```
cd ~
git clone https://github.com/moggieuk/Happy-Hare.git
cd ~/Happy-Hare
./install.sh -i
```
**Select MMU:** Pick option 16 - Other/Custom. <br/><br/>
<p align="center">
  Installer screen: Pick option 16 - Other/Custom
</p>

**Select MMU type:** Pick option 7 - Type-B (multiple filament drive steppers) with individual post-gear sensors, No Encoder <br/><br/>
<p align="center">
  Installer screen: Pick option 7 - Type-B with individual post-gear sensors, no encoder
</p>

**Select lane number:** Type the number of lanes you have set up. In my example below it is 8. <br/><br/>
<p align="center">
  Enter number of lanes (example: 8)
</p>

**Select the board used:** Pick option 15 - Not in list / Unknown <br/><br/>
<p align="center">
  Select board: option 15 Not in list / Unknown
</p>

**LED Support:** Enable LED support <br/><br/>
<p align="center">
  Enable LED support
</p>

**Endless Spool Support:** Enable Endless Spool support <br/><br/>
<p align="center">
  Enable Endless Spool support
</p>

**Include all the MMU config files:** Include all mmu config files in the printer.cfg <br/><br/>
<p align="center">
  Include MMU config files in printer.cfg
</p>

**(Optional) Mini 12864 screen support:** If you have a Mini 12864 screen, enabe the Happy Hare screen menu <br/><br/>
<p align="center">
  Enable Happy Hare menu for Mini 12864 (optional)
</p>

**Default pause/resume macros:** Include the default pause/resume macros from Happy Hare. Once the installation is complete, make sure you disable/remove any custom pause/resume macros that you may have in your existing Klipper installation! <br/><br/>
<p align="center">
  Include default pause/resume macros from Happy Hare
</p>

**EREC support:** Decline the installation of the EREC filament cutter <br/><br/>
<p align="center">
  Decline EREC filament cutter installation
</p>

**Moonraker.conf update:** Update your moonraker.conf as below:
```
[file_manager]
enable_object_processing: True

[mmu_server]
enable_file_preprocessor: True
enable_toolchange_next_pos: True
update_spoolman_location: True
```

<br/><br/>
Baseline setup is now complete!
<br/><br/>
## Configuring the EMU hardware in Happy Hare

### Update mmu/base/mmu.cfg
The Happy hare installer generates a generic mmu.cfg file that needs re-writing for the EMU. 

**Step 1: Clear the mmu.cfg file.** <br/><br/>
Start by completely deleting the content of that file and hitting save.

**Step 2: Update mmu.cfg with the EMU mcu boards definitions** <br/><br/>
For each lane you will need a distinct mcu mmu block defining the board name and the canbus UUID as noted earlier. In the example below I am using an 8 lane configuration.
```
[mcu mmu0]
canbus_uuid: cc8f39d714ce 
canbus_interface: can0

[mcu mmu1]
canbus_uuid: c2357f5873d7 
canbus_interface: can0

[mcu mmu2]
canbus_uuid: 31fb8c95fbfd 
canbus_interface: can0

[mcu mmu3]
canbus_uuid: 8579c5130649 
canbus_interface: can0

[mcu mmu4]
canbus_uuid: 49abda4839e6
canbus_interface: can0

[mcu mmu5]
canbus_uuid: 7d42f7c43687
canbus_interface: can0

[mcu mmu6]
canbus_uuid: 3efbe46e5d5f
canbus_interface: can0

[mcu mmu7]
canbus_uuid: f050daaa5448 
canbus_interface: can0
```

**Step 3: Update mmu.cfg with the EMU mcu board pin aliases** <br/><br/>
After the board definitions, insert the board pin aliases. 

> [!IMPORTANT]
> **Important note:** The first board defines the aliases for the tension and compression sensor too, so it is different to the rest. In the example below I am using an 8 lane configuration.
```
[board_pins mmu0]
mcu: mmu0 
aliases:
    MMU_GEAR_UART=PA15,
    MMU_GEAR_STEP=PD0,
    MMU_GEAR_DIR=PD1,
    MMU_GEAR_ENABLE=PD2,
    MMU_GEAR_DIAG=,

    MMU_NEOPIXEL=PD3,
    MMU_NEOPIXEL_LOGO=,

    MMU_PRE_GATE_0=PB7,
    MMU_POST_GEAR_0=PB5,

    MMU_TENSION=PB8, # First lane has the sync feedback sensor attached to it!
    MMU_COMPRESSION=PB9, # First lane has the sync feedback sensor attached to it!

    EJECT_BUTTON_0=PB6,

[board_pins mmu1]
mcu: mmu1 
aliases:

    MMU_GEAR_UART_1=PA15,
    MMU_GEAR_STEP_1=PD0,
    MMU_GEAR_DIR_1=PD1,
    MMU_GEAR_ENABLE_1=PD2,
    MMU_GEAR_DIAG_1=,

    MMU_PRE_GATE_1=PB7,
    MMU_POST_GEAR_1=PB5,

    EJECT_BUTTON_1=PB6,

[board_pins mmu2]
mcu: mmu2 
aliases:

    MMU_GEAR_UART_2=PA15,
    MMU_GEAR_STEP_2=PD0,
    MMU_GEAR_DIR_2=PD1,
    MMU_GEAR_ENABLE_2=PD2,
    MMU_GEAR_DIAG_2=,

    MMU_PRE_GATE_2=PB7,
    MMU_POST_GEAR_2=PB5,

    EJECT_BUTTON_2=PB6,

[board_pins mmu3]
mcu: mmu3
aliases:

    MMU_GEAR_UART_3=PA15,
    MMU_GEAR_STEP_3=PD0,
    MMU_GEAR_DIR_3=PD1,
    MMU_GEAR_ENABLE_3=PD2,
    MMU_GEAR_DIAG_3=,

    MMU_PRE_GATE_3=PB7,
    MMU_POST_GEAR_3=PB5,

    EJECT_BUTTON_3=PB6,

[board_pins mmu4]
mcu: mmu4 
aliases:

    MMU_GEAR_UART_4=PA15,
    MMU_GEAR_STEP_4=PD0,
    MMU_GEAR_DIR_4=PD1,
    MMU_GEAR_ENABLE_4=PD2,
    MMU_GEAR_DIAG_4=,

    MMU_PRE_GATE_4=PB7,
    MMU_POST_GEAR_4=PB5,

    EJECT_BUTTON_4=PB6,

[board_pins mmu5]
mcu: mmu5
aliases:

    MMU_GEAR_UART_5=PA15,
    MMU_GEAR_STEP_5=PD0,
    MMU_GEAR_DIR_5=PD1,
    MMU_GEAR_ENABLE_5=PD2,
    MMU_GEAR_DIAG_5=,

    MMU_PRE_GATE_5=PB7,
    MMU_POST_GEAR_5=PB5,

    EJECT_BUTTON_5=PB6,

[board_pins mmu6]
mcu: mmu6
aliases:

    MMU_GEAR_UART_6=PA15,
    MMU_GEAR_STEP_6=PD0,
    MMU_GEAR_DIR_6=PD1,
    MMU_GEAR_ENABLE_6=PD2,
    MMU_GEAR_DIAG_6=,

    MMU_PRE_GATE_6=PB7,
    MMU_POST_GEAR_6=PB5,

    EJECT_BUTTON_6=PB6,

[board_pins mmu7]
mcu: mmu7
aliases:

    MMU_GEAR_UART_7=PA15,
    MMU_GEAR_STEP_7=PD0,
    MMU_GEAR_DIR_7=PD1,
    MMU_GEAR_ENABLE_7=PD2,
    MMU_GEAR_DIAG_7=,

    MMU_PRE_GATE_7=PB7,
    MMU_POST_GEAR_7=PB5,

    EJECT_BUTTON_7=PB6,
```
This file is now complete! 

### Update mmu/base/mmu_hardware.cfg

**Step 1: Clear the mmu_hardware.cfg file.** <br/><br/>
Start by completely deleting the content of that file and hitting save.

**Step 2: Paste the below configuration in the mmu_hardware.cfg file**<br/><br/>
The below starter setup is for an 8 lane unit. To set up a lower lane count, paste the complete content below and change the below:
1. num_gates: 8 -> to equal to the number of lanes you have
2. Delete the unecessary tmc and stepper blocks. For example if you have a 5 lane unit, delete Filament Drive Gear_5, Filament Drive Gear_6, Filament Drive Gear_7 blocks from the below.
3. Delete the uncesessary pre_gate_switch_pin sections and post_gear_switch_pin sections. For example for a 5 lane setup, remove pre_gate_switch_pin_5, pre_gate_switch_pin_6, pre_gate_switch_pin_7, post_gear_switch_pin_5, post_gear_switch_pin_6, post_gear_switch_pin_7
4. Update the LED chain_count: 16 is for 8 lanes. This needs to be equal to number of lanes x 2. So for a 5 lane setup this would be set to 10.
5. Update the LED effect exit leds: exit_leds: neopixel:mmu_leds (1,3,5,7,9,11,13,15) is for 8 lanes. For 5, this should be 1,3,5,7,9.
6. Update the LED effect entry leds: entry_leds: neopixel:mmu_leds (2,4,6,8,10,12,14,16) is for 8 lanes. For 5, this should be 2,4,6,8,10

If you have more than 8 lanes, insert accordingly additional blocks, following the patterns as illustrated in the full configuration file below.

> [!TIP]
> If during testing you see that the EMU stepper spins backwards, invert the dir_pin by adding a ! infront of it (!dir_pin).

Finally, update your toolhead sensors definition to match your setup. Here I have the extruder entry (top) sensor in my toolhead can board named EBBCan connected to pin PB6 and the toolhead sensor (post extruder) at pin PB5.
```
extruder_switch_pin: ^EBBCan: PB6
toolhead_switch_pin: ^EBBCan: PB5
```

File contents - mmu_hardware.cfg:

```
[mmu_machine]
num_gates: 8			
mmu_vendor: Other			
mmu_version: 1.0			

selector_type: VirtualSelector
variable_bowden_lengths: 1		
variable_rotation_distances: 1		
require_bowden_move: 1		
filament_always_gripped: 1	
has_bypass: 1 

# FILAMENT DRIVE GEAR STEPPER  -----------------------------------------------------------------------------------------
[tmc2209 stepper_mmu_gear]
uart_pin: mmu0:MMU_GEAR_UART
run_current: 0.8		
hold_current: 0.2	
interpolate: False
sense_resistor: 0.110	
stealthchop_threshold: 1		

[stepper_mmu_gear]
step_pin: mmu0:MMU_GEAR_STEP
dir_pin: mmu0:MMU_GEAR_DIR
enable_pin: !mmu0:MMU_GEAR_ENABLE
rotation_distance: 22.7574		
gear_ratio: 1:1			
microsteps: 32				
full_steps_per_rotation: 200		

# Filament Drive Gear_1 --------------------------
[tmc2209 stepper_mmu_gear_1]
uart_pin: mmu1:MMU_GEAR_UART_1

[stepper_mmu_gear_1]
step_pin: mmu1:MMU_GEAR_STEP_1
dir_pin: mmu1:MMU_GEAR_DIR_1
enable_pin: !mmu1:MMU_GEAR_ENABLE_1

# Filament Drive Gear_2 --------------------------
[tmc2209 stepper_mmu_gear_2]
uart_pin: mmu2:MMU_GEAR_UART_2

[stepper_mmu_gear_2]
step_pin: mmu2:MMU_GEAR_STEP_2
dir_pin: mmu2:MMU_GEAR_DIR_2
enable_pin: !mmu2:MMU_GEAR_ENABLE_2

# Filament Drive Gear_3 --------------------------
[tmc2209 stepper_mmu_gear_3]
uart_pin: mmu3:MMU_GEAR_UART_3

[stepper_mmu_gear_3]
step_pin: mmu3:MMU_GEAR_STEP_3
dir_pin: mmu3:MMU_GEAR_DIR_3
enable_pin: !mmu3:MMU_GEAR_ENABLE_3

# Filament Drive Gear_4 --------------------------
[tmc2209 stepper_mmu_gear_4]
uart_pin: mmu4:MMU_GEAR_UART_4

[stepper_mmu_gear_4]
step_pin: mmu4:MMU_GEAR_STEP_4
dir_pin: mmu4:MMU_GEAR_DIR_4
enable_pin: !mmu4:MMU_GEAR_ENABLE_4

# Filament Drive Gear_5 --------------------------
[tmc2209 stepper_mmu_gear_5]
uart_pin: mmu5:MMU_GEAR_UART_5

[stepper_mmu_gear_5]
step_pin: mmu5:MMU_GEAR_STEP_5
dir_pin: mmu5:MMU_GEAR_DIR_5
enable_pin: !mmu5:MMU_GEAR_ENABLE_5

# Filament Drive Gear_6 --------------------------
[tmc2209 stepper_mmu_gear_6]
uart_pin: mmu6:MMU_GEAR_UART_6

[stepper_mmu_gear_6]
step_pin: mmu6:MMU_GEAR_STEP_6
dir_pin: mmu6:MMU_GEAR_DIR_6
enable_pin: !mmu6:MMU_GEAR_ENABLE_6

# Filament Drive Gear_7 --------------------------
[tmc2209 stepper_mmu_gear_7]
uart_pin: mmu7:MMU_GEAR_UART_7

[stepper_mmu_gear_7]
step_pin: mmu7:MMU_GEAR_STEP_7
dir_pin: mmu7:MMU_GEAR_DIR_7
enable_pin: !mmu7:MMU_GEAR_ENABLE_7

[mmu_sensors]
pre_gate_switch_pin_0: ^mmu0:MMU_PRE_GATE_0
pre_gate_switch_pin_1: ^mmu1:MMU_PRE_GATE_1
pre_gate_switch_pin_2: ^mmu2:MMU_PRE_GATE_2
pre_gate_switch_pin_3: ^mmu3:MMU_PRE_GATE_3
pre_gate_switch_pin_4: ^mmu4:MMU_PRE_GATE_4
pre_gate_switch_pin_5: ^mmu5:MMU_PRE_GATE_5
pre_gate_switch_pin_6: ^mmu6:MMU_PRE_GATE_6
pre_gate_switch_pin_7: ^mmu7:MMU_PRE_GATE_7

post_gear_switch_pin_0: ^mmu0:MMU_POST_GEAR_0
post_gear_switch_pin_1: ^mmu1:MMU_POST_GEAR_1
post_gear_switch_pin_2: ^mmu2:MMU_POST_GEAR_2
post_gear_switch_pin_3: ^mmu3:MMU_POST_GEAR_3
post_gear_switch_pin_4: ^mmu4:MMU_POST_GEAR_4
post_gear_switch_pin_5: ^mmu5:MMU_POST_GEAR_5
post_gear_switch_pin_6: ^mmu6:MMU_POST_GEAR_6
post_gear_switch_pin_7: ^mmu7:MMU_POST_GEAR_7

extruder_switch_pin: ^EBBCan: PB6
toolhead_switch_pin: ^EBBCan: PB5

sync_feedback_tension_pin: ^mmu0:MMU_TENSION         # Compression is when you pull the bowden tubes (entry/exit) away from each other. Tension when you push the tubes together.
sync_feedback_compression_pin: ^mmu0:MMU_COMPRESSION

# MMU NEOPIXEL LED SUPPORT ------------------------------------------------------------------------------------

[neopixel mmu_leds]
pin: mmu0:MMU_NEOPIXEL
chain_count: 16			# Number lanes x2
color_order: GRBW		# Set based on your particular neopixel specification

# MMU LED EFFECT SEGMENTS ----------------------------------------------------------------------------------------------

[mmu_leds unit0]
exit_leds:   neopixel:mmu_leds (1,3,5,7,9,11,13,15) # First, third, fifth LED and so forth.
entry_leds: neopixel:mmu_leds (2,4,6,8,10,12,14,16) # Second, fourth, sixth LED and so forth.
logo_leds:    
frame_rate: 24

enabled: True                           # LEDs are enabled at startup
animation: True                         # Use led-animation-effects
exit_effect: gate_status                # gate_status in the eject buttons
entry_effect: filament_color            # filament_color in the dry box LED
status_effect: off                      # no status LED is on the unit
logo_effect: (0, 0, 0)                  # no Logo LED is on the unit
white_light: (1, 1, 1)                  # RGB color for static white light
black_light: (1, 1, 1)                  # RGB color used to represent "black" filament
empty_light: (0.0, 0.0, 0.0)            # Empty gate has eject button "off"

effect_loading:            mmu_blue_clockwise_slow, (0, 0, 0.4)
effect_loading_extruder:   mmu_blue_clockwise_fast, (0, 0, 1)
effect_unloading:          mmu_blue_anticlock_slow, (0, 0, 0.4)
effect_unloading_extruder: mmu_blue_anticlock_fast, (0, 0, 1)
effect_heating:            mmu_breathing_red,       (0.3, 0, 0)
effect_selecting:          mmu_white_fast,          (0.2, 0.2, 0.2)
effect_checking:           mmu_white_fast,          (0.8, 0.8, 0.8)
effect_initialized:        mmu_rainbow,             (0.5, 0.2, 0)
effect_error:              mmu_strobe,              (1, 0, 0)
effect_complete:           mmu_sparkle,             (0.3, 0.3, 0.3)
effect_gate_selected:      mmu_static_blue,         (0, 0, 1)
effect_gate_available:     mmu_static_white_dim,    (0.3, 0.3, 0.3)
effect_gate_available_sel: mmu_ready_white,         (0.75, 0.75, 0.75)
effect_gate_unknown:       mmu_static_orange,       (0.5, 0.2, 0)
effect_gate_unknown_sel:   mmu_ready_orange,        (0.75, 0.3, 0)
effect_gate_empty:         mmu_static_black,        (0, 0, 0)
effect_gate_empty_sel:     mmu_ready_red,           (0.2, 0, 0)
```

Add the below custom LED effect colors at the bottom of your **printer.cfg**. These are used in the LED effects above.

```
[mmu_led_effect mmu_static_white_dim]
define_on:    gates
layers:       static 0 0 top (0.3,0.3,0.3)

[mmu_led_effect mmu_ready_white]
define_on:    gates
layers:       breathing 2 0 subtract (0.4,0.4,0.4)
              static 0 0 top (0.5,0.5,0.5)

[mmu_led_effect mmu_ready_red]
define_on:    gates
layers:       breathing 2 0 subtract (0.4,0.0,0.0)
              static 0 0 top (0.5,0.0,0.0)
```

### Update mmu/addons/mmu_eject_buttons_hw.cfg
**Step 1: Clear the mmu_eject_buttons_hw.cfg file.** <br/><br/>
Start by completely deleting the content of that file and hitting save.

**Step 2: Paste the below configuration in the mmu_eject_buttons_hw.cfg file**<br/><br/>
The below starter setup is for an 8 lane unit. To set up a lower lane count, paste the complete content below and delete the corresponding [gcode_button mmu_eject_button_N] sections. If you have more than 8 lanes, add more blocks following the patterns below.
```
[gcode_button mmu_eject_button_0]
pin: mmu0:EJECT_BUTTON_0
press_gcode: _MMU_EJECT_BUTTON GATE=0

[gcode_button mmu_eject_button_1]
pin: mmu1:EJECT_BUTTON_1
press_gcode: _MMU_EJECT_BUTTON GATE=1

[gcode_button mmu_eject_button_2]
pin: mmu2:EJECT_BUTTON_2
press_gcode: _MMU_EJECT_BUTTON GATE=2

[gcode_button mmu_eject_button_3]
pin: mmu3:EJECT_BUTTON_3
press_gcode: _MMU_EJECT_BUTTON GATE=3

[gcode_button mmu_eject_button_4]
pin: mmu4:EJECT_BUTTON_4
press_gcode: _MMU_EJECT_BUTTON GATE=4

[gcode_button mmu_eject_button_5]
pin: mmu5:EJECT_BUTTON_5
press_gcode: _MMU_EJECT_BUTTON GATE=5

[gcode_button mmu_eject_button_6]
pin: mmu6:EJECT_BUTTON_6
press_gcode: _MMU_EJECT_BUTTON GATE=6

[gcode_button mmu_eject_button_7]
pin: mmu7:EJECT_BUTTON_7
press_gcode: _MMU_EJECT_BUTTON GATE=7
```

### Update printer.cfg
We will be updating the printer.cfg to add support for the BME humidity sensors as below. Similarly to the other files, remove or add the temperature sensor blocks to match your lane count.

```
[temperature_sensor Lane_0]
sensor_type: BME280
i2c_address: 118
i2c_mcu: mmu0
i2c_software_scl_pin: mmu0:PB3
i2c_software_sda_pin: mmu0:PB4

[temperature_sensor Lane_1]
sensor_type: BME280
i2c_address: 118
i2c_mcu: mmu1
i2c_software_scl_pin: mmu1:PB3
i2c_software_sda_pin: mmu1:PB4

[temperature_sensor Lane_2]
sensor_type: BME280
i2c_address: 118
i2c_mcu: mmu2
i2c_software_scl_pin: mmu2:PB3
i2c_software_sda_pin: mmu2:PB4

[temperature_sensor Lane_3]
sensor_type: BME280
i2c_address: 118
i2c_mcu: mmu3
i2c_software_scl_pin: mmu3:PB3
i2c_software_sda_pin: mmu3:PB4

[temperature_sensor Lane_4]
sensor_type: BME280
bme280_report_time: 20
i2c_address: 118
i2c_mcu: mmu4
i2c_software_scl_pin: mmu4:PB3
i2c_software_sda_pin: mmu4:PB4

[temperature_sensor Lane_5]
sensor_type: BME280
i2c_address: 118
i2c_mcu: mmu5
i2c_software_scl_pin: mmu5:PB3
i2c_software_sda_pin: mmu5:PB4

[temperature_sensor Lane_6]
sensor_type: BME280
bme280_report_time: 20
i2c_address: 118
i2c_mcu: mmu6
i2c_software_scl_pin: mmu6:PB3
i2c_software_sda_pin: mmu6:PB4

[temperature_sensor Lane_7]
sensor_type: BME280
i2c_address: 118
i2c_mcu: mmu7
i2c_software_scl_pin: mmu7:PB3
i2c_software_sda_pin: mmu7:PB4
```

### Save, restart and confirm lanes are visible
Once all of the above steps are completed hit save and restart klipper. The MMU hardware should now all be set up and all your lanes visible in the machine panel as below:

<p align="center">
  Installer screen
</p>

## Configuring Happy Hare
Now that the hardware is set up and visible to klipper, the next step is to configure the Happy Hare software to match the EMU capabilities and general Type B MMU good practice. That configuration will be predominately done in the mmu/base/mmu_parameters.cfg file. The indicated configuration below is geared towards reliability of feeding vs. filament swap speed. Use that as a starting point and tune to your liking once the unit is fully configured and operational.

### Setting up the EMU software parameters in mmu/base/mmu_parameters.cfg
Unlike the hardware setup files, do not delete the content of this file. We will be making targeted changes to match the EMU capabilities as validated through our testing.

**MMU Hardware Limits:** The EMU can operate up to a maximum of 500mm/sec feeding velocity and 400mm/sec2 acceleration. Adjust the maximum hardware limits as below.</br>
```
gear_max_velocity: 500
gear_max_accel: 400
```
**Logging:** Reduce log verbosity to reduce SD Card wear and system load</br></br>
```
log_level: 1
log_file_level: 1		
log_statistics: 0 		
log_visual: 1			
log_startup_status: 1		
log_m117_messages: 1
```			
**Speeds:** Our objective is reliability with operation. While the EMU can operate at 500mm/sec feeding, any snag in the filament path risks the lane stepper skipping steps. As such, it is recommended that conservative values are used in the speed set up, and tune up from there.</br>
```
gear_from_spool_speed: 200
gear_from_spool_accel: 100
gear_from_buffer_speed: 200
gear_from_buffer_accel: 100
gear_unload_speed: 200
gear_unload_accel: 100

gear_short_move_speed: 100
gear_short_move_accel: 100
gear_short_move_threshold: 100
gear_homing_speed: 100

extruder_load_speed: 16
extruder_unload_speed: 20
extruder_sync_load_speed: 16
extruder_sync_unload_speed: 20
extruder_homing_speed: 16

macro_toolhead_max_accel: 0
macro_toolhead_min_cruise_ratio: 0.5
```
**Gate load:** The EMU uses the post stepper (gear) switch sensor as the filament homing point for the lanes. That means that when swapping colors, the filament will retract all the way into the EMU dry box. This has three benefits which maximise flexibility in lane / base unit arrangements and reliability in feeding filament:
1. The filament is kept as dry as possible as it is now fully in the dry box. This results in lower probability of the filament snapping in the lane stepper gear due to it absorbing humidity from the environment.
2. There is no need for a sensor at the combiner, simplifying wiring setup and configuration.
3. You can expand to as many lanes as you want with any combination of passive combiners to bring the lane bowden tubes together to one that feeds the toolhead.

The downside is that the full bowden length needs to be traversed when loading, resulting in slightly longer loading times (however that is almost insignificant) and that the bowden length for each lane needs to be calibrated before first use (this is an automated process described later in this guide).

In addition, conservative homing max and preload homing max value have been selected, to allow the user time to load the filament and ensure it is gripped by the EMU lane stepper. 

It is therefore recommended to use the below values as is and do not modify unless trying to troubleshoot a specific issue.</br>
```
gate_homing_endstop: mmu_gear	
gate_homing_max: 600
gate_preload_homing_max: 600
gate_preload_parking_distance: 2
gate_unload_buffer: 50
gate_parking_distance: 2          # park the filament 2mm before the stepper exit switch. Do not increase this value beyond this as you are then risking the filament walking past the stepper gears.
gate_autoload: 1
gate_final_eject_distance: 100
```
**Bowden load:** As the EMU can accomodate long bowden tubes feeding to the printer, the bowden_homing_max is increased to allow Happy Hare to feed a longer run. 

In addition the correction and unload test moves are disabled as the encoder is not fitted in the base setup. From experience, encoders tend to accumulate dust after a few thousand swap cycles requiring ongoing maintenance. In addition they materially elevate the noise profile of the unit and add a point of "filament impact" in the bowden loading path.</br>
```
bowden_homing_max: 3000	# if the EMU lane to toolhead distance is larger than 3 meters, increase this value.

bowden_apply_correction: 0	
bowden_allowable_load_delta: 10.0

bowden_pre_unload_test: 0	
bowden_pre_unload_error_tolerance: 60 
```
**Extruder homing:** The below values are tuned to improve overall feeding reliability. The extruder homing max value has been increased, allowing for slight slippage during the bowden load to be compensated for. In addition, the homing buffer has been increased reducing the fast load speed 50mm before the filament arrives at the toolhead, to reduce possibility of filament impacting the gears.</br>
```
extruder_homing_max: 400			# Larger than the default HH value. This allows for homing to complete even if the filament skips steps during the load/
extruder_homing_endstop: extruder	
extruder_homing_buffer: 50
extruder_collision_homing_current: 100

extruder_force_homing: 0
```
**Toolhead Load:** This section needs to be populated following toolhead dimension calibration. Starter values from the community are available here: https://link.3dcoded.xyz/tipconfigs/ . 

In addition, the below settings have been adjusted to allow more tolerance in case of the extruder delaying grabbing the filament, which improves feeding reliability and allows for more "flex" in a slightly miss-tuned setup</br>
```
toolhead_homing_max: 250			# Increased from default of 40, to allow more tolerance in the extruder not grabbing the filament immediately.
toolhead_unload_safety_margin: 50	# Increased from the default of 10, to ensure filament is for sure clear of the extruder during unload.
toolhead_post_load_tighten: 0		# this is ignored as EMU is a Type B MMU - set to 0
toolhead_post_load_tension_adjust: 1	# Adjust tension post load to attemt to centre the sync feedback sensor. 
toolhead_entry_tension_test: 0		# Not required - toolhead sensor ensures feeding has happened.
```
**Tip Forming:** A toolhead cutter is highly recommended. Venture into tip forming at your own risk!</br>
```
force_form_tip_standalone: 1		  # Always standalone tip forming (TURN SLICER OFF!)
form_tip_macro: _MMU_CUT_TIP	
extruder_form_tip_current: 130		  # Bump up extruder current during tip forming. Helps ensure no skipped steps on the extruder if cutting is not 100% clean
slicer_tip_park_pos: 0			      # This specifies the position of filament in extruder after slicer completes tip forming. (TURN SLICER TIP FORMING OFF!)
```
**Purging:** If you have the blobifier set up, enable it here. For a baseline, starter setup, the below is recommended. Setting up the blobifier is recommended to be done after this guide is complete and your first test print is completed successfully.</br>
```
force_purge_standalone: 0 		# Use slicer purging (purge block) - set to 1 for blobifier
purge_macro: _MMU_PURGE			# Replace this with BLOBIFIER when set up
extruder_purge_current: 100		# leave this unchanged. If the extruder is skipping during purging with the blobifier you are most likely exceeding your hotend flow limit.
```
**Motor sync:** Setup sync feedback sensor (EMUSync) here. The sync multiplier high and low values allow for +/- 10% tolerance in rotation distance variation between your EMU lane and your extruder. If you find you need more than this for the unit to stay in sync then most likely either your extruder or EMU lane is not calibrated correctly.</br>
```
sync_gear_current: 80			    # 80% EMU stepper current during printing -> 0.64A
sync_feedback_enabled: 1		    # Enable EMU Sync sync feedback sensor
sync_feedback_buffer_range: 12		# EMU Sync switch to switch distance
sync_feedback_buffer_maxrange: 25	# EMU Sync max travel
sync_multiplier_high: 1.10		    # over-feed by 10% when in tension
sync_multiplier_low: 0.90		    # under-feed by 10% when in compression
```
**Filament Management:** Disable clog detection (as the encoder is not fitted to the unit) and enable endless spool (automated failover to the next available spool as defined in the gate map, administered via the Mainsail UI or Klipperscreen).</br>
```
enable_clog_detection: 0		
enable_endless_spool: 1			    # enable endless spool
endless_spool_on_load: 0	
endless_spool_eject_gate: -1		# Eject filament in the current gate
```
Here you can also configure spoolman filament management (highly recommended - instructions here:https://github.com/moggieuk/Happy-Hare/wiki/Spoolman-Support). </br></br>

**Calibration:** While happy hare can auto calibrate both the bowden tube length and lane rotation distance, I personally recommend a manual calibration for run to run consistency. Therefore all automated calibrations are disabled to ensure run-to-run consistency.</br>
```
autocal_bowden_length: 0	# Disable automated bowden length calibration
autotune_bowden_length: 0	# Disable automated bowden length tuning
skip_cal_rotation_distance: 0	# Require gate rotation distance calibration
autotune_rotation_distance: 0	# Disable automated gate calibration/tuning.
skip_cal_encoder: 0		# Encoder not fitted
autotune_encoder: 0		# Encoder not fitted
```

**Misc:** Minor options tuning and instructing Happy Hare that a filamentalist rewinder is used instead of a buffer </br>
```
timeout_pause: 86400		    # Idle time out in seconds. Set to 24 hours, to allow you to react and fix a pause if a swap issue materialises.
disable_heater: 60		        # Disable the hotend heater 60 seconds after an error is detected to reduce oozing.
default_extruder_temp: 230	    # Default temperature for performing swaps and forming tips when not in print (overridden by gate map). 230C is a good all around temperature for most material types.
extruder_temp_variance: 30	    # When waiting for extruder temperature this is the +/- permissible variance in degrees (>= 1).

startup_home_if_unloaded: 0	    # 0 = do nothing
startup_reset_ttg_map: 0	    #  0 = do nothing
show_error_dialog: 0		    # 0 = show error in console only. No mainsail pop-up
preload_attempts: 5		        # How many "grabbing" attempts are made to pick up the filament with preload feature
strict_filament_recovery: 0	    # If enabled with MMU with toolhead sensor, this will cause filament position recovery to
                                # perform extra moves to look for filament trapped in the space after extruder but before sensor
                                # This is largely uncessary but can be enabled if your toolhead setup is not particularly reliable.
filament_recovery_on_pause: 1	# Run a quick check to determine current filament position on pause/error.
retry_tool_change_on_error: 1	# Automatically retry a failed tool change. While this may mask a unit issue, we are aiming for relability during print.
bypass_autoload: 1		        # If extruder sensor fitted, this controls the automatic loading of extruder for bypass operation
has_filament_buffer: 0          # We are using a Filamentalist so no separate filament buffer is installed
#
# Advanced options. Don't mess unless you fully understand. Read documentation.
#
encoder_move_validation: 0	     # ADVANCED: 1 = Normally Encoder validates move distances are within given tolerance
                                 #           0 = Validation is disabled (eliminates slight pause between moves but less safe)
print_start_detection: 1	     # ADVANCED: Enabled for Happy Hare to automatically detect start and end of print and call
                                 # ADVANCED: MMU_PRINT_START and MMU_PRINT_END automatically. Harmless to leave enabled but can disable
                                 #           if you think it is causing problems and known START/END is covered in your macros
extruder: extruder		         # ADVANCED: Name of the toolhead extruder that MMU is using
gcode_load_sequence: 0		     # VERY ADVANCED: Gcode loading sequence 1=enabled, 0=internal logic (default)
gcode_unload_sequence: 0	     # VERY ADVANCED: Gcode unloading sequence, 1=enabled, 0=internal logic (default)
```

**Klipper:** Enable klipper timer too close (TTC) mitigations.</br>
```
update_trsync: 1		    # 1 = Increase TRSYNC_TIMEOUT, 0 = Leave the klipper default
canbus_comms_retries: 3		# Number of retries. Recommend the default of 3.
update_bit_max_time: 1		# 1 = Increase BIT_MAX_TIME, 0 = Leave the klipper default
update_aht10_commands: 0	# BTT ViViD specific setting. Leave at 0.
```

### Setting up the EMU software parameters in mmu/base/mmu_macro_vars.cfg
Unlike the hardware setup files, do not delete the content of this file. The below are some common settings that I have found usefull to change from default. However, the **detailed guide on Happy hare must be followed to set up your cut tip macro and to configure the system for your specific printer setup**. For more read here: https://github.com/moggieuk/Happy-Hare/wiki/Configuring-mmu_macro_vars.cfg

> [!WARNING]
> **WARNING: DO NOT RUN A PRINT WITHOUT CONFIGURING THE ABOVE.** The stock cut tip macro will most likely not work for your setup and you will crash the hotend on the cutter.

```
variable_min_toolchange_z       : 15.0 # Be safe and dont scratch the bed
variable_park_travel_speed      : 450  # Travel a bit faster to avoid stringing
```

## Calibrating the unit
Now that the baseline software is set up, the unit needs to be calibrated. There are 2 key calibrations that need to be done before the unit allows you to print.
1. Lane rotation distance
2. Bowden length per lane

Detailed instructions can be found here: https://github.com/moggieuk/Happy-Hare/wiki/MMU-Calibration-TypeB . The below will outline the mandatory minimum steps to calibrate the unit.

### Lane rotation distance calibration
Before you start with this calibration, remove all bowden tubes from the rear of the dry boxes going to the combiner. Add a short length of PTFE tubing (50mm is enough) to the first lane dry box exit. This will help guide the filament and not grind on the ecas connector. Then proceed to load some filament and execute the below instructions to grip it and feed it.

**Step 1:** Select the gate, load filament and move 200mm (or more) till the filament is showing from the unit exit ECAS connector.
```
MMU_SELECT GATE=0
MMU_TEST_MOVE MOVE=200 # run this once or more till you get filament out from the dry box.
```
**Step 2:** Cut the end of the filament poking out from the short ptfe tube attached to the dry box flush with the ptfe tube. Run the below command:
```
MMU_TEST_MOVE MOVE=100
```
Cut the filament again flush with the ptfe tube attached to the dry box. Measure it. Now use the below command to calibrate the rotation distance of the box.
```
MMU_CALIBRATE_GEAR MEASURED=102.5 #102.5 is an example value and should correspond to the value measured.
```
**Step 3:** Repeat for all lanes
```
MMU_SELECT GATE=1 # then 2,3,4, etc etc.
MMU_TEST_MOVE MOVE=200 # run this once or more till you get filament out from the dry box.
..... cut the filament at the box ptfe tube exit .....
MMU_TEST_MOVE MOVE=100
MMU_CALIBRATE_GEAR MEASURED=102.5 #102.5 is an example value and should correspond to the value measured.
```

> [!IMPORTANT]
> If you observe significant variation between gates, double check that your BMG gears are centred with the filament path and that the tension is approximately as equal as possible between them.

Rotation distance calibration is now done! 

### Bowden tube calibration
Now remove the short PTFE tube from the rear of the dry box and connect the combiner and your bowden tube to the EMU Sync and from there to the toolhead. The final calibration is to measure the length of bowden tube from the lane filament parking location to the toolhead. These will be different for each lane, hence these need to be individually calibrated following the procedure below.

> [!IMPORTANT]
> **IMPORTANT:** When calibrating bowden length for each lane, it is mandatory to keep the EMUSync manually held in the tension position, ie the two tubes brought towards each other. Why? The bowden calibration measures how much filament the lane feeds till the toolhead entry sensor is triggered. If the EMU Sync is left free, the springs can unpredictably compress/expand resulting in incorrect calibration. In addition, holding the EMU Sync in tension means the bowden length is slightly shorter. This helps avoid scenarios where the filament hits against the extruder if the lane rotation distance is slightly off.

```
MMU_SELECT GATE=0
MMU_CALIBRATE_BOWDEN
```
Repeat this for each lane, for example:
```
MMU_SELECT GATE=1 # then 2,3,4, etc etc.
MMU_CALIBRATE_BOWDEN
```
The unit calibration is now done and the unit is ready to be used!

## First start up
Follow the below first start up procedure to validate correct wiring of the EMU.

1. Load filament to each gate. The filament should be parked right before the post stepper sensor. In the UI, verify that the MMU Pre Gate sensor for the lane is marked as **detected** and the MMU Gear sensor for the lane is marked as **empty**. If not, you have them wired backwards. Swap their position in the mmu_hardware.cfg file.
2. Run the MMU_TEST_MOVE MOVE=50 command. Verify that the MMU Gear sensor for the lane is marked as **detected**. If not, you may have a wire break in the system.
3. Press the eject button. The filament should now be ejected from the unit. If not, you may have a wire break in the system.
4. Verify that the LEDs change color as the filament is inserted. From off to white for the eject button and off to white (if not using spoolman) for the led inside the box. If not, you may have either a power issue to the LED's or the in-out wiring sequence in the LED chain is wrong.
5. Validate your sync feedback sensor wiring. Bring the two sides of the bowden tube together. The tension switch should be showing as **detected** in the UI. Move the two sides of the bowden tube away from each other till the switch clicks. The compression switch should be showing as **detected** in the UI. If not, you have them wired backwards. Swap their position in the mmu_hardware.cfg file.
6. Home the printer, load filament to the first lane and type T0. The hotend should heat up to 230C and load filament to the toolhead. If the filament crashes to the extruder entry, your bowden distance calibration is off. If there is excessive material coming out of the nozzle, the toolhead calibration is off.

**After you have setup your Cut Tip macro** parameters:
1. Type MMU_UNLOAD. The toolhead should cut the filament and rewind to the EMU.
2. If the toolhead fails to cut, the cut tip macro is not configured correctly

## Next Steps
Finally you have to set up your slicer to recognise and operate with a multi-material unit. More instructions can be found here: https://github.com/moggieuk/Happy-Hare/wiki/Slicer-Setup

Optionally you can also set up:
1. Klipper screen integration: https://github.com/moggieuk/Happy-Hare/wiki/KlipperScreen
2. Mainsail / Fluid MMU panel: https://github.com/moggieuk/Happy-Hare/wiki/Mainsail-Fluidd-Integration
3. Spoolman: https://github.com/moggieuk/Happy-Hare/wiki/Spoolman-Support

## Seeking help

The Happy Hare discord is a great resource to help you going. Both in the general channel as well as the dedicated EMU channel. Link to the discord can be found here: https://discord.gg/aABQUjkZPk

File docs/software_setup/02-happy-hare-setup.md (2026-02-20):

# Happy Hare Setup Guide

This is a provisional sofware setup guide for the EMU using Happy Hare v3. This guide is meant to be read in conjunction with the Happy Hare setup guide as found here: https://github.com/moggieuk/Happy-Hare/wiki

## Table of Contents

- [Installing Happy Hare](#installing-happy-hare)
- [Configuring the EMU hardware](#configuring-the-emu-hardware)
- [Configuring Happy Hare parameters](#configuring-happy-hare-parameters)
- [Configuring PFS and Flowguard](#configuring-pfs-and-flowguard)
- [EMUSync PFS insights](#emusync-pfs-insights)

## Installing Happy Hare
Install Happy Hare. More detailed instructions can be found here: https://github.com/moggieuk/Happy-Hare/wiki/Installation
```
cd ~
git clone https://github.com/moggieuk/Happy-Hare.git
cd ~/Happy-Hare
./install.sh -i
```
**Select MMU:** Pick option 16 - Other/Custom. <br/><br/>
<p align="center">
  Installer screen: Pick option 16 - Other/Custom
</p>

**Select MMU type:** Pick option 7 - Type-B (multiple filament drive steppers) with individual post-gear sensors, No Encoder <br/><br/>
<p align="center">
  Installer screen: Pick option 7 - Type-B with individual post-gear sensors, no encoder
</p>

**Select lane number:** Type the number of lanes you have set up. In my example below it is 8. <br/><br/>
<p align="center">
  Enter number of lanes (example: 8)
</p>

**Select the board used:** Pick option 15 - Not in list / Unknown <br/><br/>
<p align="center">
  Select board: option 15 Not in list / Unknown
</p>

**LED Support:** Enable LED support <br/><br/>
<p align="center">
  Enable LED support
</p>

**Endless Spool Support:** Enable Endless Spool support <br/><br/>
<p align="center">
  Enable Endless Spool support
</p>

**Include all the MMU config files:** Include all mmu config files in the printer.cfg <br/><br/>
<p align="center">
  Include MMU config files in printer.cfg
</p>

**(Optional) Mini 12864 screen support:** If you have a Mini 12864 screen, enabe the Happy Hare screen menu <br/><br/>
<p align="center">
  Enable Happy Hare menu for Mini 12864 (optional)
</p>

**Default pause/resume macros:** Include the default pause/resume macros from Happy Hare. Once the installation is complete, make sure you disable/remove any custom pause/resume macros that you may have in your existing Klipper installation! <br/><br/>
<p align="center">
  Include default pause/resume macros from Happy Hare
</p>

**EREC support:** Decline the installation of the EREC filament cutter <br/><br/>
<p align="center">
  Decline EREC filament cutter installation
</p>

**Moonraker.conf update:** Make sure your moonraker.conf contains [mmu_server] (should be inserted by HappyHare setup). Update it as per the below if it doesn't match:
```
[file_manager]
enable_object_processing: True

[mmu_server]
enable_file_preprocessor: True
enable_toolchange_next_pos: True
update_spoolman_location: True
```

<br/><br/>
Baseline setup is now complete!
<br/><br/>
## Configuring the EMU hardware

### Update mmu/base/mmu.cfg
The Happy hare installer generates a generic mmu.cfg file that needs re-writing for the EMU. 

**Step 1: Clear the mmu.cfg file.** <br/><br/>
Start by completely deleting the content of that file and hitting save.

**Step 2: Update mmu.cfg with the EMU mcu boards definitions** <br/><br/>
For each lane you will need one distinct mcu mmu block defining the board name and the canbus UUID as noted earlier. In the example below I am using an 8 lane configuration. For a two lane setup, for example, you'd use `[mcu mmu0]` and `[mcu mmu1]` only.
```
[mcu mmu0]
canbus_uuid: your uuid 
canbus_interface: can0 # if you have multiple canbus buses, define here which canbus has the EMU units on it.

[mcu mmu1]
canbus_uuid: your uuid  
canbus_interface: can0

[mcu mmu2]
canbus_uuid: your uuid  
canbus_interface: can0

[mcu mmu3]
canbus_uuid: your uuid  
canbus_interface: can0

[mcu mmu4]
canbus_uuid: your uuid 
canbus_interface: can0

[mcu mmu5]
canbus_uuid: your uuid 
canbus_interface: can0

[mcu mmu6]
canbus_uuid: your uuid 
canbus_interface: can0

[mcu mmu7]
canbus_uuid: your uuid  
canbus_interface: can0
```

**Step 3: Update mmu.cfg with the EMU mcu board pin aliases** <br/><br/>
After the board definitions, insert the board pin aliases. 

> [!IMPORTANT]
> **Important note:** The first board defines the aliases for the tension and compression sensor too, so it is different to the rest. In the example below I am using an 8 lane configuration. Remove the corresponding `mmuN` reference from the mcu line to match the number of lanes you have (eg. `mcu: mmu0, mmu1` for a two lane setup).
```
[board_pins mmu]
mcu: mmu0, mmu1, mmu2, mmu3, mmu4, mmu5, mmu6, mmu7
aliases:
    MMU_GEAR_UART=PA15,
    MMU_GEAR_STEP=PD0,
    MMU_GEAR_DIR=PD1,
    MMU_GEAR_ENABLE=PD2,
    MMU_GEAR_DIAG=,

    MMU_NEOPIXEL=PD3,
    MMU_NEOPIXEL_LOGO=,

    MMU_PRE_GATE=PB7,
    MMU_POST_GEAR=PB5,

    MMU_TENSION=PB8,
    MMU_COMPRESSION=PB9,

    MMU_TH=PA3,

    MMU_FAN=PA0,

    EJECT_BUTTON=PB6,
```
This file is now complete! 

### Update mmu/base/mmu_hardware.cfg

**Step 1: Clear the mmu_hardware.cfg file.** <br/><br/>
Start by completely deleting the content of that file and hitting save.

**Step 2: Paste the below configuration in the mmu_hardware.cfg file**<br/><br/>
The below starter setup is for an 8 lane unit. To set up a lower lane count, paste the complete content below and change the below:
1. **num_gates: 8 -> to equal to the number of lanes you have**
2. **Delete the unecessary tmc and stepper blocks**. For example if you have a 5 lane unit, delete `[tmc2209 stepper_mmu_gear_5]`, `[tmc2209 stepper_mmu_gear_6]`, `[tmc2209 stepper_mmu_gear_7]` blocks from the below.
3. **Delete the uncesessary pre_gate_switch_pin lines and post_gear_switch_pin lines**. For example for a 5 lane setup, remove `pre_gate_switch_pin_5`, `pre_gate_switch_pin_6`, `pre_gate_switch_pin_7`, `post_gear_switch_pin_5`, `post_gear_switch_pin_6`, `post_gear_switch_pin_7`
4. **Delete the uncesessary LED blocks**: add or remove `[neopixel mmuN_leds]` to match your number of lanes
5. ***Delete the uncesessary LED effect exit leds**: Add / remove `neopixel:mmuN_leds (2)` and `neopixel:mmuN_leds (1)` from the corresponding entry and exit sections in the `[mmu_leds unit0]` block.

If you have more than 8 lanes, insert accordingly additional blocks, following the patterns illustrated in the full configuration file below.

> [!TIP]
> If during testing you see that the EMU stepper spins backwards, invert the dir_pin by adding a ! infront of it (!dir_pin).

Finally, update your toolhead sensors definition to match your setup. Here I have the extruder entry (top) sensor in my toolhead can board named EBBCan connected to pin PB6 and the toolhead sensor (post extruder) at pin PB5.
```
extruder_switch_pin: ^EBBCan: PB6
toolhead_switch_pin: ^EBBCan: PB5
```

File contents - mmu_hardware.cfg:

```
[mmu_machine]
num_gates: 8			
mmu_vendor: EMU			
mmu_version: 1.0			

selector_type: VirtualSelector
variable_bowden_lengths: 1		
variable_rotation_distances: 1		
require_bowden_move: 1		
filament_always_gripped: 1	
has_bypass: 1 

# Add your temperature and humidity sensors here for them to be visible in mainsail. One line per lane.
# Supported in HH vesion 3.42 and above.
environment_sensors:   temperature_sensor Lane_0, 
						            temperature_sensor Lane_1,
                        temperature_sensor Lane_2,
                        temperature_sensor Lane_3,
                        temperature_sensor Lane_4,
                        temperature_sensor Lane_5,
                        temperature_sensor Lane_6,
                        temperature_sensor Lane_7 

# FILAMENT DRIVE GEAR STEPPER  -----------------------------------------------------------------------------------------
[tmc2209 stepper_mmu_gear]
uart_pin: mmu0:MMU_GEAR_UART
run_current: 0.8		
hold_current: 0.2	
interpolate: False
sense_resistor: 0.110	
stealthchop_threshold: 1		

[stepper_mmu_gear]
step_pin: mmu0:MMU_GEAR_STEP
dir_pin: mmu0:MMU_GEAR_DIR
enable_pin: !mmu0:MMU_GEAR_ENABLE
rotation_distance: 22.7574		
gear_ratio: 1:1			
microsteps: 32				
full_steps_per_rotation: 200		

# Filament Drive Gear_1 --------------------------
[tmc2209 stepper_mmu_gear_1]
uart_pin: mmu1:MMU_GEAR_UART

[stepper_mmu_gear_1]
step_pin: mmu1:MMU_GEAR_STEP
dir_pin: mmu1:MMU_GEAR_DIR
enable_pin: !mmu1:MMU_GEAR_ENABLE

# Filament Drive Gear_2 --------------------------
[tmc2209 stepper_mmu_gear_2]
uart_pin: mmu2:MMU_GEAR_UART

[stepper_mmu_gear_2]
step_pin: mmu2:MMU_GEAR_STEP
dir_pin: mmu2:MMU_GEAR_DIR
enable_pin: !mmu2:MMU_GEAR_ENABLE

# Filament Drive Gear_3 --------------------------
[tmc2209 stepper_mmu_gear_3]
uart_pin: mmu3:MMU_GEAR_UART

[stepper_mmu_gear_3]
step_pin: mmu3:MMU_GEAR_STEP
dir_pin: mmu3:MMU_GEAR_DIR
enable_pin: !mmu3:MMU_GEAR_ENABLE

# Filament Drive Gear_4 --------------------------
[tmc2209 stepper_mmu_gear_4]
uart_pin: mmu4:MMU_GEAR_UART

[stepper_mmu_gear_4]
step_pin: mmu4:MMU_GEAR_STEP
dir_pin: mmu4:MMU_GEAR_DIR
enable_pin: !mmu4:MMU_GEAR_ENABLE

# Filament Drive Gear_5 --------------------------
[tmc2209 stepper_mmu_gear_5]
uart_pin: mmu5:MMU_GEAR_UART

[stepper_mmu_gear_5]
step_pin: mmu5:MMU_GEAR_STEP
dir_pin: mmu5:MMU_GEAR_DIR
enable_pin: !mmu5:MMU_GEAR_ENABLE

# Filament Drive Gear_6 --------------------------
[tmc2209 stepper_mmu_gear_6]
uart_pin: mmu6:MMU_GEAR_UART

[stepper_mmu_gear_6]
step_pin: mmu6:MMU_GEAR_STEP
dir_pin: mmu6:MMU_GEAR_DIR
enable_pin: !mmu6:MMU_GEAR_ENABLE

# Filament Drive Gear_7 --------------------------
[tmc2209 stepper_mmu_gear_7]
uart_pin: mmu7:MMU_GEAR_UART

[stepper_mmu_gear_7]
step_pin: mmu7:MMU_GEAR_STEP
dir_pin: mmu7:MMU_GEAR_DIR
enable_pin: !mmu7:MMU_GEAR_ENABLE

[mmu_sensors]
pre_gate_switch_pin_0: ^mmu0:MMU_PRE_GATE
pre_gate_switch_pin_1: ^mmu1:MMU_PRE_GATE
pre_gate_switch_pin_2: ^mmu2:MMU_PRE_GATE
pre_gate_switch_pin_3: ^mmu3:MMU_PRE_GATE
pre_gate_switch_pin_4: ^mmu4:MMU_PRE_GATE
pre_gate_switch_pin_5: ^mmu5:MMU_PRE_GATE
pre_gate_switch_pin_6: ^mmu6:MMU_PRE_GATE
pre_gate_switch_pin_7: ^mmu7:MMU_PRE_GATE

post_gear_switch_pin_0: ^mmu0:MMU_POST_GEAR
post_gear_switch_pin_1: ^mmu1:MMU_POST_GEAR
post_gear_switch_pin_2: ^mmu2:MMU_POST_GEAR
post_gear_switch_pin_3: ^mmu3:MMU_POST_GEAR
post_gear_switch_pin_4: ^mmu4:MMU_POST_GEAR
post_gear_switch_pin_5: ^mmu5:MMU_POST_GEAR
post_gear_switch_pin_6: ^mmu6:MMU_POST_GEAR
post_gear_switch_pin_7: ^mmu7:MMU_POST_GEAR

extruder_switch_pin: ^EBBCan: PB6
toolhead_switch_pin: ^EBBCan: PB5

# Section below if using the dual switch version of the EMU Sync. 
sync_feedback_tension_pin: ^mmu0:MMU_TENSION         # Compression is when you pull the bowden tubes (entry/exit) away from each other. Tension when you push the tubes together.
sync_feedback_compression_pin: ^mmu0:MMU_COMPRESSION

# Section below if using the Proportional (PFS) version of the EMU Sync. Run the calibration routine (MMU_CALIBRATE_PSENSOR) and
# update the sync_feedback_analog_max_compression, sync_feedback_analog_max_tension and sync_feedback_analog_neutral_point accordingly.
# Comment out/delete the dual switch section above and uncomment the section below to use.
#sync_feedback_analog_pin: mmu0:MMU_TH
#sync_feedback_analog_max_compression: 0.9435
#sync_feedback_analog_max_tension:     0.0982
#sync_feedback_analog_neutral_point:   0.5275

# MMU NEOPIXEL LED SUPPORT ------------------------------------------------------------------------------------

[neopixel mmu0_leds] # one block per lane (Lane 0)
pin: mmu0:MMU_NEOPIXEL
chain_count: 2			# one for the box and one for the eject button
color_order: GRBW		

[neopixel mmu1_leds] # one block per lane (Lane 1)
pin: mmu1:MMU_NEOPIXEL
chain_count: 2			
color_order: GRBW		

[neopixel mmu2_leds] # one block per lane (Lane 2)
pin: mmu2:MMU_NEOPIXEL
chain_count: 2		
color_order: GRBW	

[neopixel mmu3_leds] # one block per lane (Lane 3)
pin: mmu3:MMU_NEOPIXEL
chain_count: 2			
color_order: GRBW

[neopixel mmu4_leds] # one block per lane (Lane 4)
pin: mmu4:MMU_NEOPIXEL
chain_count: 2			
color_order: GRBW

[neopixel mmu5_leds] # one block per lane (Lane 5)
pin: mmu5:MMU_NEOPIXEL
chain_count: 2			
color_order: GRBW

[neopixel mmu6_leds] # one block per lane (Lane 6)
pin: mmu6:MMU_NEOPIXEL
chain_count: 2			
color_order: GRBW

[neopixel mmu7_leds] # one block per lane (Lane 7)
pin: mmu7:MMU_NEOPIXEL
chain_count: 2			
color_order: GRBW	

# MMU LED EFFECT SEGMENTS ----------------------------------------------------------------------------------------------
[mmu_leds unit0]
exit_leds:
  neopixel:mmu0_leds (1) # add/remove to match number of lanes
  neopixel:mmu1_leds (1)
  neopixel:mmu2_leds (1)
  neopixel:mmu3_leds (1)
  neopixel:mmu4_leds (1)
  neopixel:mmu5_leds (1)
  neopixel:mmu6_leds (1)
  neopixel:mmu7_leds (1)
entry_leds:
  neopixel:mmu0_leds (2) # add/remove to match number of lanes
  neopixel:mmu1_leds (2)
  neopixel:mmu2_leds (2)
  neopixel:mmu3_leds (2)
  neopixel:mmu4_leds (2)
  neopixel:mmu5_leds (2)
  neopixel:mmu6_leds (2)
  neopixel:mmu7_leds (2)
frame_rate: 24

enabled: True                           # LEDs are enabled at startup
animation: True                         # Use led-animation-effects
exit_effect: gate_status                # gate_status in the eject buttons
entry_effect: filament_color            # filament_color in the dry box LED
status_effect: off                      # no status LED is on the unit
logo_effect: (0, 0, 0)                  # no Logo LED is on the unit
white_light: (1, 1, 1)                  # RGB color for static white light
black_light: (1, 1, 1)                  # RGB color used to represent "black" filament
empty_light: (0.0, 0.0, 0.0)            # Empty gate has eject button "off"

effect_loading:            mmu_blue_clockwise_slow, (0, 0, 0.4)
effect_loading_extruder:   mmu_blue_clockwise_fast, (0, 0, 1)
effect_unloading:          mmu_blue_anticlock_slow, (0, 0, 0.4)
effect_unloading_extruder: mmu_blue_anticlock_fast, (0, 0, 1)
effect_heating:            mmu_breathing_red,       (0.3, 0, 0)
effect_selecting:          mmu_white_fast,          (0.2, 0.2, 0.2)
effect_checking:           mmu_white_fast,          (0.8, 0.8, 0.8)
effect_initialized:        mmu_rainbow,             (0.5, 0.2, 0)
effect_error:              mmu_strobe,              (1, 0, 0)
effect_complete:           mmu_sparkle,             (0.3, 0.3, 0.3)
effect_gate_selected:      mmu_static_blue,         (0, 0, 1)
effect_gate_available:     mmu_static_white_dim,    (0.3, 0.3, 0.3)
effect_gate_available_sel: mmu_ready_white,         (0.75, 0.75, 0.75)
effect_gate_unknown:       mmu_static_orange,       (0.5, 0.2, 0)
effect_gate_unknown_sel:   mmu_ready_orange,        (0.75, 0.3, 0)
effect_gate_empty:         mmu_static_black,        (0, 0, 0)
effect_gate_empty_sel:     mmu_ready_red,           (0.2, 0, 0)
```

### Update mmu/addons/mmu_eject_buttons_hw.cfg
**Step 1: Clear the mmu_eject_buttons_hw.cfg file.** <br/><br/>
Start by completely deleting the content of that file and hitting save.

**Step 2: Paste the below configuration in the mmu_eject_buttons_hw.cfg file**<br/><br/>
The below starter setup is for an 8 lane unit. To set up a lower lane count, paste the complete content below and delete the corresponding `[gcode_button mmu_eject_button_N]` sections. If you have more than 8 lanes, add more blocks following the patterns below.
```
[gcode_button mmu_eject_button_0]
pin: mmu0:EJECT_BUTTON
press_gcode: _MMU_EJECT_BUTTON GATE=0

[gcode_button mmu_eject_button_1]
pin: mmu1:EJECT_BUTTON
press_gcode: _MMU_EJECT_BUTTON GATE=1

[gcode_button mmu_eject_button_2]
pin: mmu2:EJECT_BUTTON
press_gcode: _MMU_EJECT_BUTTON GATE=2

[gcode_button mmu_eject_button_3]
pin: mmu3:EJECT_BUTTON
press_gcode: _MMU_EJECT_BUTTON GATE=3

[gcode_button mmu_eject_button_4]
pin: mmu4:EJECT_BUTTON
press_gcode: _MMU_EJECT_BUTTON GATE=4

[gcode_button mmu_eject_button_5]
pin: mmu5:EJECT_BUTTON
press_gcode: _MMU_EJECT_BUTTON GATE=5

[gcode_button mmu_eject_button_6]
pin: mmu6:EJECT_BUTTON
press_gcode: _MMU_EJECT_BUTTON GATE=6

[gcode_button mmu_eject_button_7]
pin: mmu7:EJECT_BUTTON
press_gcode: _MMU_EJECT_BUTTON GATE=7
```

### Upload the emu_macros.cfg file and reference it in your printer.cfg
The [linked file here](https://github.com/DW-Tas/EMU/tree/main/macros) contains a set of configurations and definitions that are required for EMU to function. In addition, it contains a fan auto control macro, to minimize noise and ensure adequate unit cooling.

Upload that file in your klipper environment and add the below line to include it in your printer.cfg file:
```[include emu_macros.cfg]```

That file contains the **BME temperature and humidity sensor definitions** as below. It is set up for an 8 lane unit, so if you have less lanes, delete the corresponding blocks from the file.
```
[temperature_sensor Lane_N]
sensor_type: BME280
i2c_address: 118
i2c_mcu: mmu0  # mmu0=First lane, mmu1=second lane etc.
i2c_software_scl_pin: mmu0:PB3
i2c_software_sda_pin: mmu0:PB4
```
It also contains the definition of the onboard EBB temperature sensors used to control the unit fans. Similarly, it is set up for an 8 lane unit, so if you have less lanes, delete the corresponding blocks from the file.
```
[temperature_sensor _Lane_N_onboard]
sensor_type: temperature_mcu
sensor_mcu: mmu0 # mmu0=First lane, mmu1=second lane etc.
min_temp: 0
max_temp: 130
```
In addition, it contains the fan definitions for the unit as below. Similarly, it is set up for an 8 lane unit, so if you have less lanes, delete the corresponding blocks from the file.
```
[fan_generic _emu_fan_N]
pin: mmu0:MMU_FAN # mmu0=First lane, mmu1=second lane etc.
max_power: 1
kick_start_time: 0.5
```
Finally it contains the fan control macro that controls the fans on a by-lane basis. In the variable_sensors add the names of the **_Lane_N_onboard temperature sensors**, separated by a comma. In the variable_fans add the names of the **base unit fans**, separated by a comma. 

> [!NOTE]
> Prefixing the fans and board temperature sensors with a _ will hide them from the Mainsail UI, which is helpful to reduce clutter once you have your setup tuned and validated.

> [!IMPORTANT]
> The length of these two lists must match and correspond to each other (ie lane 0 fan and lane 0 onboard temp sensor must be first on the list etc).
> Make sure you include the **onboard temperature sensors in the fan control macro, not the BME sensors!**

Finally you can set the temperature where the fans turn on and off. By default, they are set to turn on at 39C and turn off at 37C.

```[gcode_macro MMU_FAN_CFG]
description: Holds configuration/state for multi fan controller.
variable_on_temp: 39.0
variable_off_temp: 37.0
variable_poll_s: 5.0
variable_enabled: True
variable_forced: -1                 # -1=AUTO, 0=all OFF, 1=all ON (global)
variable_sensors: "_Lane_0_onboard,_Lane_1_onboard,_Lane_2_onboard,_Lane_3_onboard,_Lane_4_onboard,_Lane_5_onboard,_Lane_6_onboard,_Lane_7_onboard"   # Comma-separated temperature_sensor names
variable_fans:    "_emu_fan_0,_emu_fan_1,_emu_fan_2,_emu_fan_3,_emu_fan_4,_emu_fan_5,_emu_fan_6,_emu_fan_7"  # Comma-separated fan_generic names
variable_warned_len_mismatch: False # internal: warn once per enable
gcode:
```
That file also contains some bespoke LED effects for the EMU, which are used earlier in the LED setup section.

### Save, restart and confirm lanes are visible
Once all of the above steps are completed hit save and restart klipper. The MMU hardware should now all be set up and all your lanes visible in the machine panel as below:

<p align="center">
  Installer screen
</p>

## Configuring Happy Hare parameters
Now that the hardware is set up and visible to klipper, the next step is to configure the Happy Hare software to match the EMU capabilities and general Type B MMU good practice. That configuration will be predominately done in the mmu/base/mmu_parameters.cfg file. The indicated configuration below is geared towards reliability of feeding vs. filament swap speed. Use that as a starting point and tune to your liking once the unit is fully configured and operational.

### Setting up the EMU software parameters in mmu/base/mmu_parameters.cfg
Unlike the hardware setup files, do not delete the content of this file. We will be making targeted changes to match the EMU capabilities as validated through our testing.

**MMU Hardware Limits:** The EMU can operate up to a maximum of 500mm/sec feeding velocity and 400mm/sec2 acceleration. Adjust the maximum hardware limits as below.</br>
```
gear_max_velocity: 500
gear_max_accel: 400
```
**Logging:** Reduce log verbosity to reduce SD Card wear and system load</br></br>
```
log_level: 1
log_file_level: 1		
log_statistics: 0 		
log_visual: 1			
log_startup_status: 1		
log_m117_messages: 1
```			
**Speeds:** Our objective is reliability with operation. While the EMU can operate at 500mm/sec feeding, any snag in the filament path risks the lane stepper skipping steps. As such, it is recommended that conservative values are used in the speed set up, and tune up from there.</br>
```
gear_from_spool_speed: 250
gear_from_spool_accel: 120
#gear_from_buffer_speed: 250 # This is not necessary. Delete this line as there is no buffer.
#gear_from_buffer_accel: 120 # This is not necessary. Delete this line as there is no buffer.
gear_unload_speed: 250
gear_unload_accel: 120

gear_short_move_speed: 100
gear_short_move_accel: 100
gear_short_move_threshold: 100
gear_homing_speed: 100

extruder_load_speed: 16
extruder_unload_speed: 20
extruder_sync_load_speed: 16
extruder_sync_unload_speed: 20
extruder_homing_speed: 16

macro_toolhead_max_accel: 0
macro_toolhead_min_cruise_ratio: 0.5
```
**Gate load:** The EMU uses the post stepper (gear) switch sensor as the filament homing point for the lanes. That means that when swapping colors, the filament will retract all the way into the EMU dry box. This has three benefits which maximise flexibility in lane / base unit arrangements and reliability in feeding filament:
1. The filament is kept as dry as possible as it is now fully in the dry box. This results in lower probability of the filament snapping in the lane stepper gear due to it absorbing humidity from the environment.
2. There is no need for a sensor at the combiner, simplifying wiring setup and configuration.
3. You can expand to as many lanes as you want with any combination of passive combiners to bring the lane bowden tubes together to one that feeds the toolhead.

The downside is that the full bowden length needs to be traversed when loading, resulting in slightly longer loading times (however that is almost insignificant) and that the bowden length for each lane needs to be calibrated before first use (this is an automated process described later in this guide).

In addition, conservative homing max and preload homing max value have been selected, to allow the user time to load the filament and ensure it is gripped by the EMU lane stepper. 

It is therefore recommended to use the below values as is and do not modify unless trying to troubleshoot a specific issue.</br>
```
gate_homing_endstop: mmu_gear	
gate_homing_max: 600
gate_preload_homing_max: 600
gate_preload_parking_distance: 1
gate_unload_buffer: 100
gate_parking_distance: 1          # park the filament 1mm before the stepper exit switch. Do not increase this value beyond this as you are then risking the filament walking past the stepper gears.
gate_autoload: 1
gate_final_eject_distance: 100
```
**Bowden load:** As the EMU can accomodate long bowden tubes feeding to the printer, the bowden_homing_max is increased to allow Happy Hare to feed a longer run. 

In addition the correction and unload test moves are disabled as the encoder is not fitted in the base setup. From experience, encoders tend to accumulate dust after a few thousand swap cycles requiring ongoing maintenance. In addition they materially elevate the noise profile of the unit and add a point of "filament impact" in the bowden loading path.</br>
```
bowden_homing_max: 3000	# if the EMU lane to toolhead distance is larger than 3 meters, increase this value.

bowden_apply_correction: 0	
bowden_allowable_load_delta: 10.0

bowden_pre_unload_test: 0	
bowden_pre_unload_error_tolerance: 60 
```
**Extruder homing:** The below values are tuned to improve overall feeding reliability. The extruder homing max value has been increased, allowing for slight slippage during the bowden load to be compensated for. In addition, the homing buffer has been increased reducing the fast load speed 50mm before the filament arrives at the toolhead, to reduce possibility of filament impacting the gears.</br>
```
extruder_homing_max: 400			# Larger than the default HH value. This allows for homing to complete even if the filament skips steps during the load/
extruder_homing_endstop: extruder	
extruder_homing_buffer: 50
extruder_collision_homing_current: 100

extruder_force_homing: 0
```
**Toolhead Load:** This section needs to be populated following toolhead dimension calibration. Starter values from the community are available here: https://link.3dcoded.xyz/tipconfigs/ . 

In addition, the below settings have been adjusted to allow more tolerance in case of the extruder delaying grabbing the filament, which improves feeding reliability and allows for more "flex" in a slightly miss-tuned setup</br>
```
toolhead_homing_max: 250			# Increased from default of 40, to allow more tolerance in the extruder not grabbing the filament immediately.
toolhead_unload_safety_margin: 90	# Increased from the default of 10, to ensure filament is for sure clear of the extruder during unload.
toolhead_post_load_tighten: 0		# this is ignored as EMU is a Type B MMU - set to 0
toolhead_post_load_tension_adjust: 1	# Adjust tension post load to attemt to centre the sync feedback sensor. 
toolhead_entry_tension_test: 0		# Not required - toolhead sensor ensures feeding has happened.
```
**Tip Forming:** A toolhead cutter is highly recommended. Venture into tip forming at your own risk!</br>
```
force_form_tip_standalone: 1		  # Always standalone tip forming (TURN SLICER OFF!)
form_tip_macro: _MMU_CUT_TIP	
extruder_form_tip_current: 130		  # Bump up extruder current during tip forming. Helps ensure no skipped steps on the extruder if cutting is not 100% clean
slicer_tip_park_pos: 0			      # This specifies the position of filament in extruder after slicer completes tip forming. (TURN SLICER TIP FORMING OFF!)
```
**Purging:** If you have the blobifier set up, enable it here. For a baseline, starter setup, the below is recommended. Setting up the blobifier is recommended to be done after this guide is complete and your first test print is completed successfully.</br>
```
force_purge_standalone: 0 		# Use slicer purging (purge block) - set to 1 for blobifier
purge_macro: 			            # Replace this with BLOBIFIER when set up. Leave empty if not using the blobifier. 
extruder_purge_current: 100		# leave this unchanged. If the extruder is skipping during purging with the blobifier you are most likely exceeding your hotend flow limit.
```
**Motor sync:** Setup sync feedback sensor (EMUSync) here. The sync multiplier high and low values allow for +/- 10% tolerance in rotation distance variation between your EMU lane and your extruder. If you find you need more than this for the unit to stay in sync then most likely either your extruder or EMU lane is not calibrated correctly.</br>
```
sync_gear_current: 50			    # 50% EMU stepper current during printing -> ~0.4A when printing. Higher than 0.5A can cause PLA to clog the EMU stepper in hot environments.
sync_feedback_enabled: 1		    # Enable EMU Sync sync feedback sensor
sync_feedback_buffer_range: 12		# EMU Sync switch to switch distance
sync_feedback_buffer_maxrange: 25	# EMU Sync max travel
sync_multiplier_high: 1.10		    # over-feed by 10% when in tension
sync_multiplier_low: 0.90		    # under-feed by 10% when in compression
```
**Filament Management:** Disable clog detection (as the encoder is not fitted to the unit) and enable endless spool (automated failover to the next available spool as defined in the gate map, administered via the Mainsail UI or Klipperscreen).</br>
```
enable_clog_detection: 0		
enable_endless_spool: 1			    # enable endless spool
endless_spool_on_load: 0	
endless_spool_eject_gate: -1		# Eject filament in the current gate
```
Here you can also configure spoolman filament management (highly recommended - instructions here:https://github.com/moggieuk/Happy-Hare/wiki/Spoolman-Support). </br></br>

**Calibration:** While happy hare can auto calibrate both the bowden tube length and lane rotation distance, I personally recommend a manual calibration for run to run consistency. Therefore all automated calibrations are disabled to ensure run-to-run consistency.</br>
```
autocal_bowden_length: 0	# Disable automated bowden length calibration
autotune_bowden_length: 0	# Disable automated bowden length tuning
skip_cal_rotation_distance: 0	# Require gate rotation distance calibration
autotune_rotation_distance: 0	# Disable automated gate calibration/tuning.
skip_cal_encoder: 0		# Encoder not fitted
autotune_encoder: 0		# Encoder not fitted
```

**Misc:** Minor options tuning and instructing Happy Hare that a filamentalist rewinder is used instead of a buffer </br>
```
timeout_pause: 86400		    # Idle time out in seconds. Set to 24 hours, to allow you to react and fix a pause if a swap issue materialises.
disable_heater: 60		        # Disable the hotend heater 60 seconds after an error is detected to reduce oozing.
default_extruder_temp: 230	    # Default temperature for performing swaps and forming tips when not in print (overridden by gate map). 230C is a good all around temperature for most material types.
extruder_temp_variance: 30	    # When waiting for extruder temperature this is the +/- permissible variance in degrees (>= 1).

startup_home_if_unloaded: 0	    # 0 = do nothing
startup_reset_ttg_map: 0	    #  0 = do nothing
show_error_dialog: 0		    # 0 = show error in console only. No mainsail pop-up
preload_attempts: 5		        # How many "grabbing" attempts are made to pick up the filament with preload feature
strict_filament_recovery: 0	    # If enabled with MMU with toolhead sensor, this will cause filament position recovery to
                                # perform extra moves to look for filament trapped in the space after extruder but before sensor
                                # This is largely uncessary but can be enabled if your toolhead setup is not particularly reliable.
filament_recovery_on_pause: 1	# Run a quick check to determine current filament position on pause/error.
retry_tool_change_on_error: 1	# Automatically retry a failed tool change. While this may mask a unit issue, we are aiming for relability during print.
bypass_autoload: 1		        # If extruder sensor fitted, this controls the automatic loading of extruder for bypass operation
has_filament_buffer: 0          # We are using a Filamentalist so no separate filament buffer is installed
#
# Advanced options. Don't mess unless you fully understand. Read documentation.
#
encoder_move_validation: 0	     # ADVANCED: 1 = Normally Encoder validates move distances are within given tolerance
                                 #           0 = Validation is disabled (eliminates slight pause between moves but less safe)
print_start_detection: 1	     # ADVANCED: Enabled for Happy Hare to automatically detect start and end of print and call
                                 # ADVANCED: MMU_PRINT_START and MMU_PRINT_END automatically. Harmless to leave enabled but can disable
                                 #           if you think it is causing problems and known START/END is covered in your macros
extruder: extruder		         # ADVANCED: Name of the toolhead extruder that MMU is using
gcode_load_sequence: 0		     # VERY ADVANCED: Gcode loading sequence 1=enabled, 0=internal logic (default)
gcode_unload_sequence: 0	     # VERY ADVANCED: Gcode unloading sequence, 1=enabled, 0=internal logic (default)
```

**Klipper:** Enable klipper timer too close (TTC) mitigations.</br>
```
update_trsync: 1		    # 1 = Increase TRSYNC_TIMEOUT, 0 = Leave the klipper default
canbus_comms_retries: 3		# Number of retries. Recommend the default of 3.
update_bit_max_time: 1		# 1 = Increase BIT_MAX_TIME, 0 = Leave the klipper default
update_aht10_commands: 0	# BTT ViViD specific setting. Leave at 0.
```

### Setting up the EMU software parameters in mmu/base/mmu_macro_vars.cfg
Unlike the hardware setup files, do not delete the content of this file. The below are some common settings that I have found usefull to change from default. However, the **detailed guide on Happy hare must be followed to set up your cut tip macro and to configure the system for your specific printer setup**. For more read here: https://github.com/moggieuk/Happy-Hare/wiki/Configuring-mmu_macro_vars.cfg

> [!WARNING]
> **WARNING: DO NOT RUN A PRINT WITHOUT CONFIGURING THE ABOVE.** The stock cut tip macro will most likely not work for your setup and you will crash the hotend on the cutter.

```
variable_min_toolchange_z       : 15.0 # Be safe and dont scratch the bed
variable_park_travel_speed      : 450  # Travel a bit faster to avoid stringing
```

## Configuring PFS and Flowguard
EMU and Happy Hare supports using a [proportional sync feedback sensor](https://github.com/DW-Tas/EMU/tree/main/STL/Tension-compression-sensor/Proportional%20Sync%20Feedback%20(PSF)%20Version) to accurately measure filament tension in the bowden tube. This is used in place of and instead of the dual switch EMUSync. The sensor [is available to purchase from Aliexpress](https://www.aliexpress.com/item/1005010470743517.html).

The proportional sensor offers the below key advantages:
1. Real time tension/compression monitoring in the bowden tube
2. Precise syncronisation between the extruder and EMU steppers
3. Real time detection of both clogs and tangles

### PFS Configuration:
The sensor is plugged in [as per the wiring diagram](https://github.com/DW-Tas/EMU/tree/main/docs/assembly_wiring#wiring-instructions-and-diagrams) - ground and signal plug into the EBB thermistor port and 5V to any unused 5V pins on the EBB.

**Step 1:** Comment out or delete the below section in the mmu_hardware.cfg file: 
```
# sync_feedback_tension_pin: ^mmu0:MMU_TENSION         # Compression is when you pull the bowden tubes (entry/exit) away from each other. Tension when you push the tubes together.
# sync_feedback_compression_pin: ^mmu0:MMU_COMPRESSION
```

**Step 2:** Uncomment or add the below section right below in the mmu_hardware.cfg file:
```
# Section below if using the Proportional (PFS) version of the EMU Sync. Run the calibration routine (MMU_CALIBRATE_PSENSOR) and
# update the sync_feedback_analog_max_compression, sync_feedback_analog_max_tension and sync_feedback_analog_neutral_point accordingly.
# Comment out/delete the dual switch section above and uncomment the section below to use.
sync_feedback_analog_pin: mmu0:MMU_TH
sync_feedback_analog_max_compression: 0.9435
sync_feedback_analog_max_tension:     0.0982
sync_feedback_analog_neutral_point:   0.5275
```
**Step 3:** Restart and test the sensor. 
1. Pull the bowden tube and expand the EMUSync PFS sensor. While holding in the expanded position run the below macro in the printer console: `MMU_QUERY_PSENSOR`.
2. Compress the sensor by pushing the ends together and run the same macro again. Record both values.
> [!IMPORTANT]
> You should see a **max raw value** greater than ~0.9 and a **min raw value** or less than ~0.1. If the values do not change when expanding and compressing the sensor recheck your wiring!

**Step 4:** Set the EMUSync dimensions in the mmu_parameters.cfg file as below. Save and restart.
```
sync_feedback_enabled: 1		
sync_feedback_buffer_range: 16		# Travel in "buffer" between compression/tension or one sensor and end
sync_feedback_buffer_maxrange: 16	# Absolute maximum end-to-end travel (mm) provided by buffer
sync_feedback_speed_multiplier: 5	# % "twolevel" gear speed delta to keep filament neutral in buffer
sync_feedback_boost_multiplier: 3	# % "twolevel" extra gear speed boost for finding initial neutral position
sync_feedback_extrude_threshold: 5	# Extruder movement (mm) for updates
```

**Step 5:** Calibrate the sensor.
1. Load filament from any lane to the toolhead using a Tx (T0,T1 etc) command.
2. In the console run `MMU_CALIBRATE_PSENSOR`
3. Note down the produced values
> [!IMPORTANT]
> If the max and min values differ significantly (>0.1) from the min and max raw values above, your calibration has failed due to excess bowden tube slack or because the sensor is getting jammed due to excess friction. Validate that the sensor moves freely and run the calibration command as follows: `MMU_CALIBRATE_PSENSOR MOVE=50`

The produced values should look like the below:
```
sync_feedback_analog_max_compression: 0.9435
sync_feedback_analog_max_tension:     0.0982
sync_feedback_analog_neutral_point:   0.5275
```

Update the corresponding values in the mmu_hardware.cfg file, save and restart.

**Step 6:** Configure flowguard (clog/tangle detection) <br/>
Edit the mmu_parameters.cfg file and amend the values below to match the suggested configuration.

```
flowguard_enabled: 1	
flowguard_max_relief: 2
flowguard_encoder_mode: 0
```
Save and restart. 

**Step 7:** You can now start a print and test the sensor in a print
1. Start a print and monitor the flowguard value in the MMU panel. It should remain close to the neutral (0) threshold
2. Expand the sensor manually - flowguard should trigger a pause. Let go, and click resume. The print should continue uninterrupted.



### EMUSync PFS insights:
You can use the sync sensor to visualise your printer's extrusion consistency, checking whether you are pushing the hotend to its limits. To do so, enable logging `sync_feedback_debug_log: 1` in the mmu_parameters.cfg file and restart. Run a print and after it is complete, execute the below command in the printer shell `~/Happy-Hare/utils/plot_sync_feedback.sh ~/printer_data/logs/sync_5.jsonl` where sync_N being the lane number in use.

You can read more on how to interpret the sync feedback telemetry data in the [Happy Hare wiki](https://github.com/moggieuk/Happy-Hare/wiki/Synchronized-Gear-Extruder#interpreting-telemetry).

**Normal telemetry data with an "unstressed" hotend** </br>
Notice how the orange line is **pretty flat and consistent**. This indicates that there is very little dynamic variation during printing between the EMU and the extruder, meaning the extruder can maintain ideal flow easily throughout the print. Also how the blue line (EMU rotation distance) converges and stabilises fairly quickly to a perfectly stable value.</br></br>


**Telemetry data showing a tangle developing towards the end of the print** </br>
Notice how the orange and blue lines slowly creep away from neutral and then flowguard (red vertical line) triggers saving the print.</br></br>
T2 sim_plot

**Telemetry data showing a hotend that is struggling to keep up with flow when printing at higher flow rates** </br>
Notice how the blue line (RD) and orange line (sensor position) rapidly deviate from neutral when an object with high flow rate is printed.</br></br>


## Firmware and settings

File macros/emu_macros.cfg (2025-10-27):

# === EMU Lane Temperature and Humidity Sensors ===

[temperature_sensor Lane_0]
sensor_type: BME280
i2c_address: 118
i2c_mcu: mmu0
i2c_software_scl_pin: mmu0:PB3
i2c_software_sda_pin: mmu0:PB4

[temperature_sensor Lane_1]
sensor_type: BME280
i2c_address: 118
i2c_mcu: mmu1
i2c_software_scl_pin: mmu1:PB3
i2c_software_sda_pin: mmu1:PB4

[temperature_sensor Lane_2]
sensor_type: BME280
i2c_address: 118
i2c_mcu: mmu2
i2c_software_scl_pin: mmu2:PB3
i2c_software_sda_pin: mmu2:PB4

[temperature_sensor Lane_3]
sensor_type: BME280
i2c_address: 118
i2c_mcu: mmu3
i2c_software_scl_pin: mmu3:PB3
i2c_software_sda_pin: mmu3:PB4

[temperature_sensor Lane_4]
sensor_type: BME280
i2c_address: 118
i2c_mcu: mmu4
i2c_software_scl_pin: mmu4:PB3
i2c_software_sda_pin: mmu4:PB4

[temperature_sensor Lane_5]
sensor_type: BME280
i2c_address: 118
i2c_mcu: mmu5
i2c_software_scl_pin: mmu5:PB3
i2c_software_sda_pin: mmu5:PB4

[temperature_sensor Lane_6]
sensor_type: BME280
i2c_address: 118
i2c_mcu: mmu6
i2c_software_scl_pin: mmu6:PB3
i2c_software_sda_pin: mmu6:PB4

[temperature_sensor Lane_7]
sensor_type: BME280
i2c_address: 118
i2c_mcu: mmu7
i2c_software_scl_pin: mmu7:PB3
i2c_software_sda_pin: mmu7:PB4


# === MMU Fan Auto-Control Configuration ===

# === Temperature sensors ===
[temperature_sensor Lane_0_onboard]
sensor_type: temperature_mcu
sensor_mcu: mmu0
min_temp: 0
max_temp: 130

[temperature_sensor Lane_1_onboard]
sensor_type: temperature_mcu
sensor_mcu: mmu1
min_temp: 0
max_temp: 130

[temperature_sensor Lane_2_onboard]
sensor_type: temperature_mcu
sensor_mcu: mmu2
min_temp: 0
max_temp: 130

[temperature_sensor Lane_3_onboard]
sensor_type: temperature_mcu
sensor_mcu: mmu3
min_temp: 0
max_temp: 130

[temperature_sensor Lane_4_onboard]
sensor_type: temperature_mcu
sensor_mcu: mmu4
min_temp: 0
max_temp: 130

[temperature_sensor Lane_5_onboard]
sensor_type: temperature_mcu
sensor_mcu: mmu5
min_temp: 0
max_temp: 130

[temperature_sensor Lane_6_onboard]
sensor_type: temperature_mcu
sensor_mcu: mmu6
min_temp: 0
max_temp: 130

[temperature_sensor Lane_7_onboard]
sensor_type: temperature_mcu
sensor_mcu: mmu7
min_temp: 0
max_temp: 130

# === Fans ===

[fan_generic emu_fan_0]
pin: mmu0:PA0
max_power: 1
kick_start_time: 0.5

[fan_generic emu_fan_1]
pin: mmu1:PA0
max_power: 1
kick_start_time: 0.5

[fan_generic emu_fan_2]
pin: mmu2:PA0
max_power: 1
kick_start_time: 0.5

[fan_generic emu_fan_3]
pin: mmu3:PA0
max_power: 1
kick_start_time: 0.5

[fan_generic emu_fan_4]
pin: mmu4:PA0
max_power: 1
kick_start_time: 0.5

[fan_generic emu_fan_5]
pin: mmu5:PA0
max_power: 1
kick_start_time: 0.5

[fan_generic emu_fan_6]
pin: mmu6:PA0
max_power: 1
kick_start_time: 0.5

[fan_generic emu_fan_7]
pin: mmu7:PA0
max_power: 1
kick_start_time: 0.5


# === MMU Fan Auto-Control (multi-sensor / multi-fan) ===
#
# Pairs each temperature sensor with a fan by index and controls
# that fan with hysteresis based on the paired sensor.
#
# Example:
#   variable_sensors: "Lane_0_onboard,Lane_0_onboard"
#   variable_fans:    "mmu_fan_0,mmu_fan_1"
#
# Notes:
# - Lists must be comma-separated names (no spaces, or strip spaces).
# - If list lengths differ, the shorter length is used (index pairing).
# - FORCE (below) is global: affects all listed fans.

[gcode_macro MMU_FAN_CFG]
description: Holds configuration/state for multi fan controller.
variable_on_temp: 39.0
variable_off_temp: 37.0
variable_poll_s: 5.0
variable_enabled: True
variable_forced: -1                 # -1=AUTO, 0=all OFF, 1=all ON (global)
variable_sensors: "Lane_0_onboard,Lane_1_onboard,Lane_2_onboard,Lane_3_onboard,Lane_4_onboard,Lane_5_onboard,Lane_6_onboard,Lane_7_onboard"   # Comma-separated temperature_sensor names
variable_fans:    "emu_fan_0,emu_fan_1,emu_fan_2,emu_fan_3,emu_fan_4,emu_fan_5,emu_fan_6,emu_fan_7"  # Comma-separated fan_generic names
variable_warned_len_mismatch: False # internal: warn once per enable
gcode:

[gcode_macro MMU_FAN_MONITOR_ENABLE]
description: Enable automatic multi-fan control.
gcode:
  SET_GCODE_VARIABLE MACRO=MMU_FAN_CFG VARIABLE=enabled VALUE=True
  UPDATE_DELAYED_GCODE ID=_MMU_FAN_LOOP DURATION=0.1
  RESPOND TYPE=echo MSG="MMU multi-fan monitor ENABLED"

[gcode_macro MMU_FAN_MONITOR_DISABLE]
description: Disable automatic control and switch all fans OFF.
gcode:
  SET_GCODE_VARIABLE MACRO=MMU_FAN_CFG VARIABLE=enabled VALUE=False
  UPDATE_DELAYED_GCODE ID=_MMU_FAN_LOOP DURATION=0
  {% set cfg = printer["gcode_macro MMU_FAN_CFG"] %}
  {% set fans = (cfg.fans|string).replace(' ','').split(',') %}
  {% for f in fans %}
    {% if f|length > 0 %}
      SET_FAN_SPEED FAN={f} SPEED=0.0
    {% endif %}
  {% endfor %}
  RESPOND TYPE=echo MSG="MMU multi-fan monitor DISABLED and all fans OFF"

[gcode_macro MMU_FAN_FORCE]
description: Global manual override for all configured fans.
# Usage:
#   MMU_FAN_FORCE S=1   -> Force ALL ON
#   MMU_FAN_FORCE S=0   -> Force ALL OFF
#   MMU_FAN_FORCE S=-1  -> Return to AUTO (per-sensor hysteresis)
gcode:
  {% set s = params.S|default(-1)|int %}
  {% if s not in [-1,0,1] %}
    RESPOND TYPE=error MSG="MMU_FAN_FORCE: S must be -1, 0, or 1"
  {% else %}
    SET_GCODE_VARIABLE MACRO=MMU_FAN_CFG VARIABLE=forced VALUE={s}
    {% set cfg = printer["gcode_macro MMU_FAN_CFG"] %}
    {% set fans = (cfg.fans|string).replace(' ','').split(',') %}
    {% if s == 1 %}
      {% for f in fans %}
        {% if f|length > 0 %}
          SET_FAN_SPEED FAN={f} SPEED=1.0
        {% endif %}
      {% endfor %}
      RESPOND TYPE=echo MSG="MMU fans FORCED ON"
    {% elif s == 0 %}
      {% for f in fans %}
        {% if f|length > 0 %}
          SET_FAN_SPEED FAN={f} SPEED=0.0
        {% endif %}
      {% endfor %}
      RESPOND TYPE=echo MSG="MMU fans FORCED OFF"
    {% else %}
      RESPOND TYPE=echo MSG="MMU fans returned to AUTO mode"
    {% endif %}
  {% endif %}

[delayed_gcode _MMU_FAN_LOOP]
initial_duration: 1
gcode:
  {% set cfg = printer["gcode_macro MMU_FAN_CFG"] %}
  {% if cfg.enabled %}
    {% set forced  = cfg.forced|int %}
    {% set on_t    = cfg.on_temp|float %}
    {% set off_t   = cfg.off_temp|float %}
    {% set sensors = (cfg.sensors|string).replace(' ','').split(',') %}
    {% set fans    = (cfg.fans|string).replace(' ','').split(',') %}
    {% set n_s     = sensors|length %}
    {% set n_f     = fans|length %}
    {% set n_min   = (n_s if n_s < n_f else n_f)|int %}

    {% if n_s != n_f and (not (cfg.warned_len_mismatch|default(False))) %}
      RESPOND TYPE=echo MSG={"MMU_FAN: sensor/fan list length mismatch"}
      SET_GCODE_VARIABLE MACRO=MMU_FAN_CFG VARIABLE=warned_len_mismatch VALUE=True
    {% endif %}

    {% if forced == 1 %}
      {% for i in range(0, n_min) %}
        {% set f = fans[i] %}
        {% if f|length > 0 %}
          SET_FAN_SPEED FAN={f} SPEED=1.0
        {% endif %}
      {% endfor %}
    {% elif forced == 0 %}
      {% for i in range(0, n_min) %}
        {% set f = fans[i] %}
        {% if f|length > 0 %}
          SET_FAN_SPEED FAN={f} SPEED=0.0
        {% endif %}
      {% endfor %}
    {% else %}
      {% for i in range(0, n_min) %}
        {% set s_name = sensors[i] %}
        {% set f = fans[i] %}
        {% if s_name|length > 0 and f|length > 0 %}
          {% set t = printer["temperature_sensor " ~ s_name].temperature|float %}
          {% set cur_speed = (printer["fan_generic " ~ f].speed|default(0.0))|float %}
          {% set cur_state = 1 if cur_speed >= 0.5 else 0 %}
          {% if cur_state == 0 %}
            {% set target_state = 1 if t >= on_t else 0 %}
          {% else %}
            {% set target_state = 1 if t > off_t else 0 %}
          {% endif %}
          {% if target_state != cur_state %}
            {% if target_state == 1 %}
              SET_FAN_SPEED FAN={f} SPEED=1.0
            {% else %}
              SET_FAN_SPEED FAN={f} SPEED=0.0
            {% endif %}
          {% endif %}
        {% endif %}
      {% endfor %}
    {% endif %}

    UPDATE_DELAYED_GCODE ID=_MMU_FAN_LOOP DURATION={cfg.poll_s}
  {% endif %}


# Happy Hare LED additions

[mmu_led_effect mmu_static_white_dim]
define_on:    gates
layers:       static 0 0 top (0.3,0.3,0.3)

[mmu_led_effect mmu_ready_white]
define_on:    gates
layers:       breathing 2 0 subtract (0.4,0.4,0.4)
              static 0 0 top (0.5,0.5,0.5)

[mmu_led_effect mmu_ready_red]
define_on:    gates
layers:       breathing 2 0 subtract (0.4,0.0,0.0)
              static 0 0 top (0.5,0.0,0.0)

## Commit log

2025-10-27 Update readme TOC with setup and calibration guide.
2025-10-27 EMU macros and configuration config file for ease of setup
    [emu_macros.cfg]
2025-12-15 Stepper and filamentalist tensioner mount updated with smoother PTFE/filametn path
2025-12-28 Updated sync gear current recommendation to mitigate potential heat creep in low flow prints using PLA
2026-01-11 Add rim rollers with square nuts
    [Rim_roller_square_nut_1_hole.step, Rim_roller_square_nut_1_hole.stl, Rim_roller_square_nut_3_holes.step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]
2026-01-23 Clarify PCB connector headers vs. BOM
2026-01-24 Update software setup pins to include proportional sensor/thermistor pins
2026-02-03 Add PCB Hatch wiring dimensions (#11)
    * Add PCB Hatch wiring dimensions
    * Fix link to Base wiring dimensions
    * Add wire lengths for old PCB board
    * Fix wiring dimension for stepper
2026-02-04 EMU Base wiring - Update pigtail motor jst diagram (#13)
    - Correct the color order of the wires
    - Add info about the two wires being swapped on one side
2026-02-05 Wiring dimensions - Update motor wiring (#15)
    Switch the green and blue wires inside the box instead of the pigtail
2026-02-07 IEMUSync mounting system
    Adding the 2020 and 4040 mounts for the filament sync unit.
    [PSF_2020_Mount_Parallel.step, PSF_2020_Mount_Parallel.stl, PSF_2020_Mount_Perpendicular.step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]
2026-02-08 Initial commit to draw io diagram for V2 wiring approach
2026-02-08 Update EMU wiring v2 (#20)
    - Update wiring for nema motors
    - Update eject button wago
2026-02-09 Updated readme with latest wiring configuration. Updated wiring diagrams
2026-02-09 Update LED definitions for revised LED wiring approach
2026-02-09 Updated temperature and humidity sensor definition in happy hare (v3.42+)
2026-02-15 Flowguard parameter tweaking
2026-02-18 Fix wiring for PFS + fix typo (#21)
2026-02-18 Multi-LED Front Button PCB and Print files
    [BOM_EMU_Multi_LED_Button_PCB_EMU_Multi_LED_Button_PCB_rev1_0.csv, Button_Filter.stl, Button_Front.stl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]
2026-02-18 Multi-LED button - correct JST plug orientation
    [Button_Filter.stl, Button_Front.stl, Button_Rear.stl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]
2026-02-18 Updated LED PCB with higher actuation force momentary switch
    [BOM_EMU_Multi_LED_Button_PCB_EMU_Multi_LED_Button_PCB_rev1_0.csv, PickAndPlace_EMU_Multi_LED_Button_PCB_rev1_0.csv]
2026-02-20 Updated flowguard parameters
2026-02-20 Flowguard updates
2026-02-24 changes of text
    [[a]_Cable_Entry-Inside_crimpable_JST.stl, [a]_Cable_Entry-Outside_crimpable_JST.stl]
2026-02-24 modified: User_Mods/EMU Cable Entry_Crimpable_JST/README.md
2026-02-24 Fix image paths in EMU Cable Entry README
    Updated image paths in README for clarity.
2026-02-24 Add inside image to README for EMU Cable Entry
    Added an image for the inside view of the EMU Cable Entry.
2026-02-24 Update README with connector links and requirements
    Added links and requirements for 3 and 4 pin connectors.

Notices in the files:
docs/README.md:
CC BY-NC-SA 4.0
